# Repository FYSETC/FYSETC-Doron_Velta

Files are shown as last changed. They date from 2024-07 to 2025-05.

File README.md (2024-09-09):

# FYSETC-Doron Velta
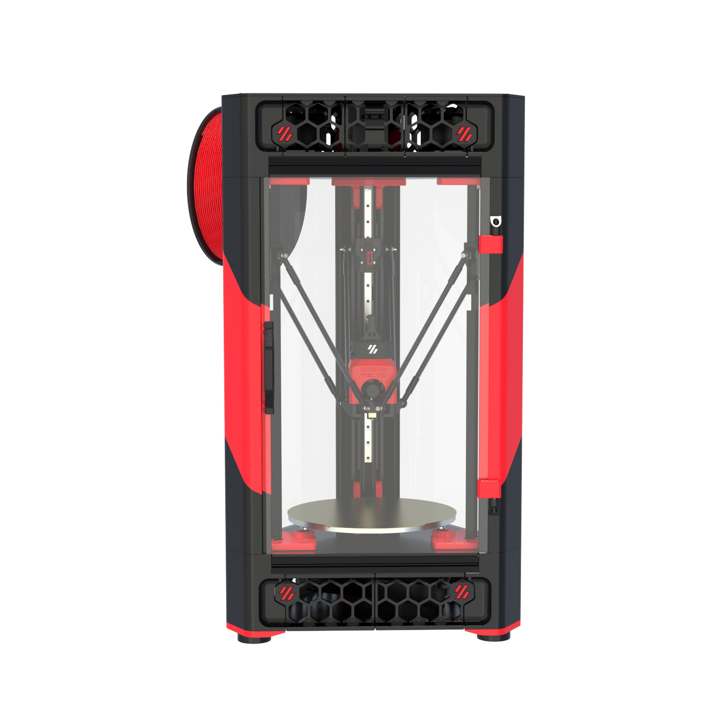
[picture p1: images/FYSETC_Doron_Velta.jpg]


## 1. Project

This is FYSETC's project database for Doron_Velta kit, which is convenient for you to find information. Thanks to rogerlz and everyone involved in this project, they always design fantastic printers.

Official Github：https://github.com/rogerlz/Doron-Velta

We make some small changes base on the Doron_Velta official material. Like change the board to R4 and others. 

## 2. Known issue

Please check your sensor cable before you power on the kit. The frst batch of sensor and endstop cables were shipped with wrong pinout. For the sensor cable, Use tweezers to change the wire on the right side of XH2.54 to the left, orthewise the sensor will be disabled.
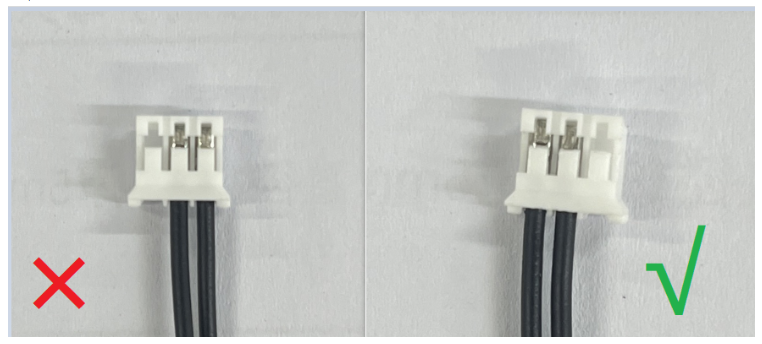
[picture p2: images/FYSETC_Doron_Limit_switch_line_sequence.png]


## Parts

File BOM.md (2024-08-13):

# Package list 

## Doron Velta 1.0

| Index | Sort | Component | Qty | Note |
| ----- | --- | --- | --- | --- |
| 1 | Fasteners | Doron Velta fasteners Pack | 1 SET  | |
| 2 | Frame | X/Y Pillars 2040 235mm | 6 PC | |
| 3 | Frame | Z Pillars 2020 500mm | 3 PCS  | |
| 4 | Motion | MGN9H Linear Rail and Carriage 350mm | 3 PCS  | |
| 5 | Motion | GATES GT2 Open Belt LL-2GT-9 (9mm wide) - 1200mm | 3 PCS  | |
| 6 | Motion | GT2 20T Pulley (5mm ID 9mm W) | 3 PCS  | |
| 7 | Motion | GT2 20T Toothed Idler (5mm ID 9mm W) | 3 PCS  | |
| 8 | Motion | Stainless steel spacer | 24 PCS | |
| 9 | Motion | Shaft Round 5x25mm (Idlers) | 3 PCS  | |
| 10 | Motion | Shaft Round 3x20mm (Bed) | 6 PCS  | |
| 11 | Motion | Washer M5x1.5mm | 8 PCS  | |
| 12 | Motion | Fisheye Rods 210mm | 6 PCS  | |
| 13 | Motion | M3 Teeth hole steel ball | 3 PCS  | |
| 14 | Vibration Management | Rubber Compressor Foot | 3 PCS  | |
| 15 | Buildplate | Aluminum plate platform - ∅200mm（Surface milling improve flatness） | 1 PCS  | |
| 16 | Buildplate | Scratch-proof Magnetic stickers ∅200mm thickness 1.5mm | 1 PCS  | |
| 17 | Buildplate | Hotbed Insulation cotton thickness 5mm | 1 PCS  | |
| 18 | Buildplate | PEI Film (∅200 mm) | 1 PCS  | |
| 19 | Buildplate | Hotbed Kit for ∅170mm 200W | 1 PCS  | |
| 20 | Controller | R4 V1.0 | 1 SET  | |
| 21 | Electronics | Raspberrypi 3B+/4B 2GB | 1 SET  | Optional |
| 22 | Electronics | MicroSD Card 16 GB | 1 PCS  | |
| 23 | Electronics | USB A to USB C - 1m | 1 PCS  | |
| 24 | Electronics | Round lamp beads | 2 PCS  | |
| 25 | Electronics | Klicky kit | 1 PCS  | |
| 26 | Electronics | Membrane level switch kit | 1 PCS  | |
| 27 | Electronics | NEMA17 Stepper motors 17HS8401 | 3 PCS  | |
| 28 | Electronics | Power Supply  Meanwell UHP-200R-24 | 1 PCS  | |
| 29 | Electronics | Raspberry Pi communication cable | 1 PCS  | |
| 30 | Electronics | Dual Ball FAN - 3010 24V (Part Fan) | 1 PCS  | |
| 31 | Electronics | Dual Ball FAN - 4010 24V(Hotend Fan) | 2 PC | |
| 32 | Electronics | Dual Ball FAN - 6020 24V (Ebox Fan) | 1 PCS  | |
| 33 | Electronics | Microswitch OMRON D2F-5 (Quickdraw Probe) with wire | 3 PCS  | |
| 34 | Electronics | Omron Solid State Relay | 1 PCS  | |
| 35 | Electronics | AC 3 Terminal Power Socket with Fuse | 1 SET  | |
| 36 | Electronics | C13 Power Cord | 1 PCS  | |
| 37 | Misc | Sherpa mini CNC Extruder | 1 SET  | |
| 38 | Misc | Wiring kit（Pre-crimped terminals and longer wire lengths with label） | 1 SET  | |
| 39 | Misc | Sailfish High Flow Hotend （ all-metal hotend 24V 60W) | 1 SET  | |
| 40 | Misc | Weaving casing 5mm 450mm | 1 PCS  | |
| 41 | Misc | Weaving casing 5mm 150mm | 2 PCS  | |
| 42 | Misc | Tension spring | 3 PCS  | |
| 43 | Misc | 4mm Bowden Coupler | 2 PCS  | |
| 44 | Misc | PTFE Tube (4mm OD 2mm ID) - 2m | 1 PCS  | |
| 45 | Misc | 6x3 Round Magnet (Quickdraw and Y Belt Set Tool) | 10 PCS | |
| 46 | Misc | Cutting pliers | 1 PCS  | |
| 47 | Misc | Hexagonal wrenchs | 1 SET  | |
| 48 | Misc | Thermal silica | 1 PCS  | |
| 49 | Misc | Ties | 30 PCS | |
| 50 | Misc | Foam Tape Thickness 3mm Length 4m | 1 PCS  | |
| 51 | Mics | The standby line 3m | 1 PCS  | |
| 52 | Misc | XH2.54 2/3/4 Pin Plastic shell | 1 SET  | |
| 53 | Panels | Bottom/Top/Electronics Bay Panels | 4 PCS  | |
| 54 | Panels | Side/Front Acrylic Panels | 3 PCS  | |

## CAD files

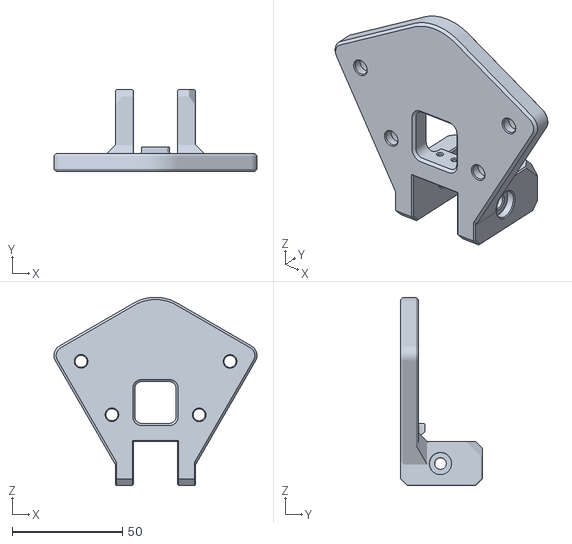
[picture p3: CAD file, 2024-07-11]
STLs/Bed Mount/Endstop Mount_x3.STL
92.1 x 37.0 x 85.5

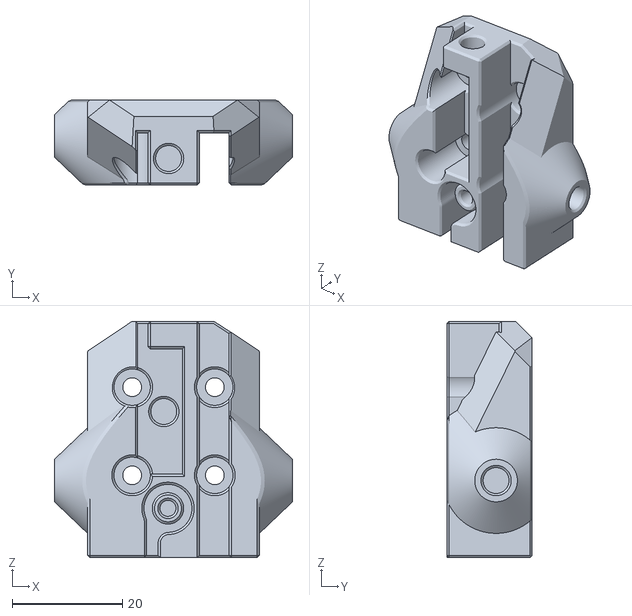
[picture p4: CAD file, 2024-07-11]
STLs/Carriage/Carriage v2_x3.STL
43.2 x 15.5 x 42.9

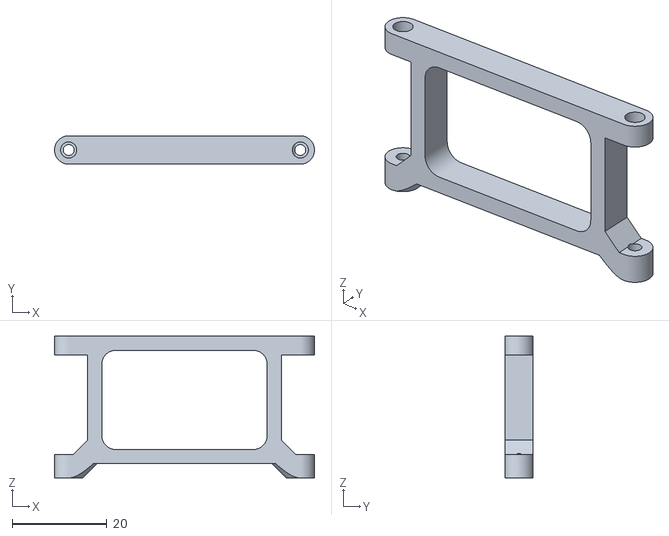
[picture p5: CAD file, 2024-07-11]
STLs/Control Board Rack/Raspberry Pi Stand_x2.STL
55.0 x 6.00 x 30.0

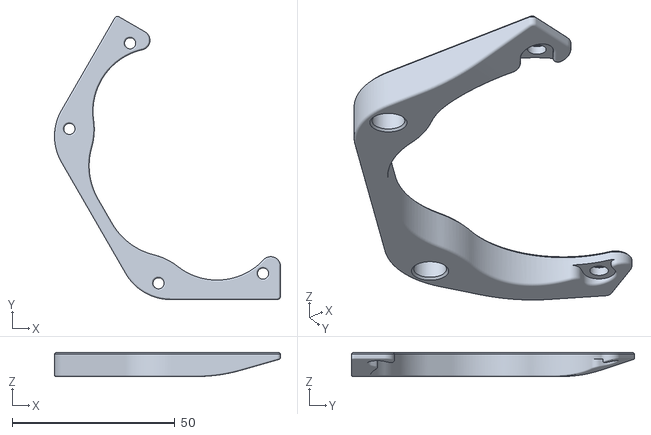
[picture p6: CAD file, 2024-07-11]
STLs/Corner Block/Foot Plate_x3.STL
69.5 x 87.1 x 7.40

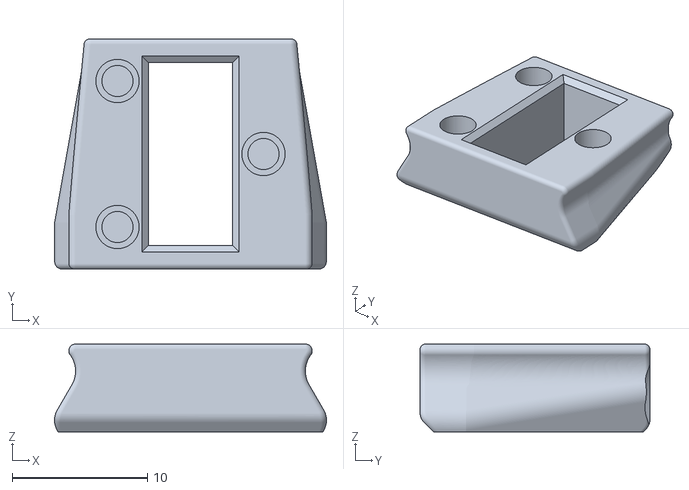
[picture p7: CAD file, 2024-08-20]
STLs/Extrude the head/printed_part.STL
20.1 x 17.0 x 6.50

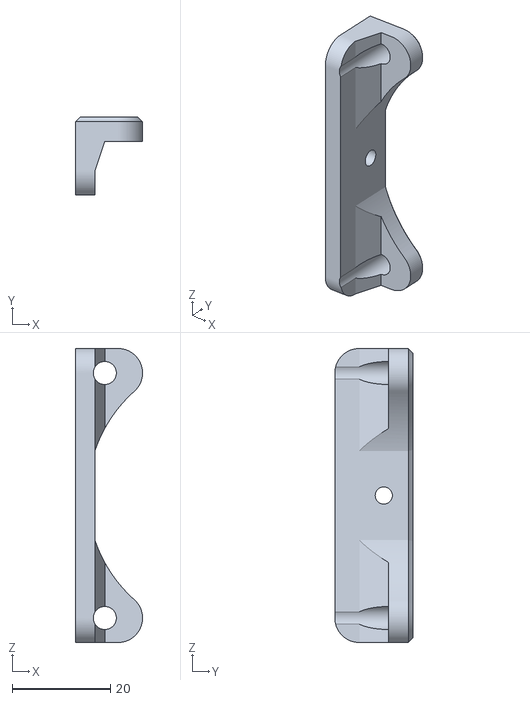
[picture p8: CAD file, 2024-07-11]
STLs/Fan/Fan Bracket_2.STL
13.7 x 16.0 x 60.0

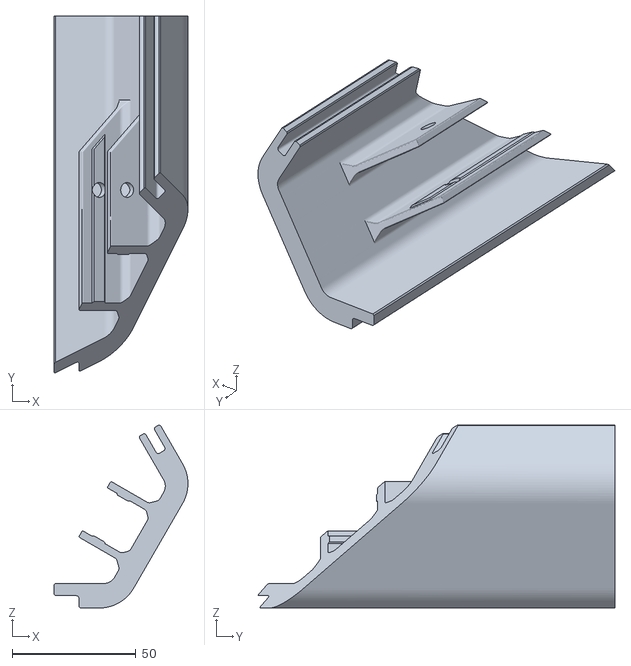
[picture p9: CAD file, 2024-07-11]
STLs/Middle Frame/Mid Corners (Mirror) Door_2_x1.STL
54.1 x 144.2 x 73.9

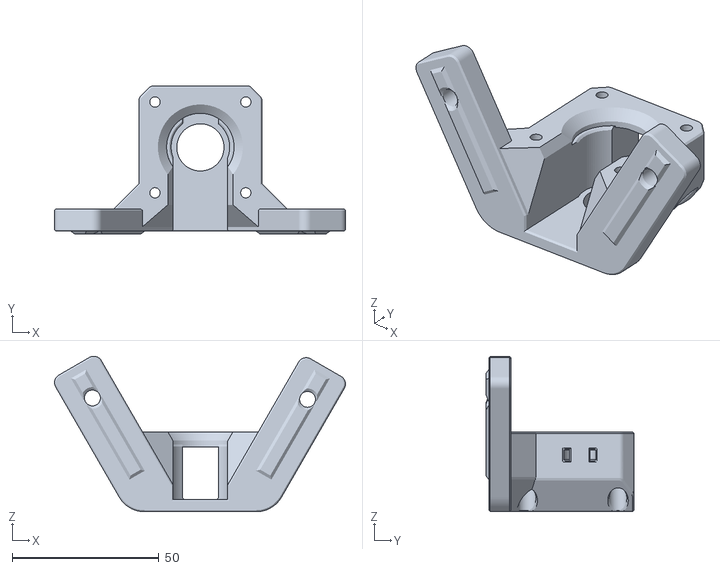
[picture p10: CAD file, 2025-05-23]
STLs/N17 Stepper Mount_x3.STL
99.3 x 50.6 x 53.0

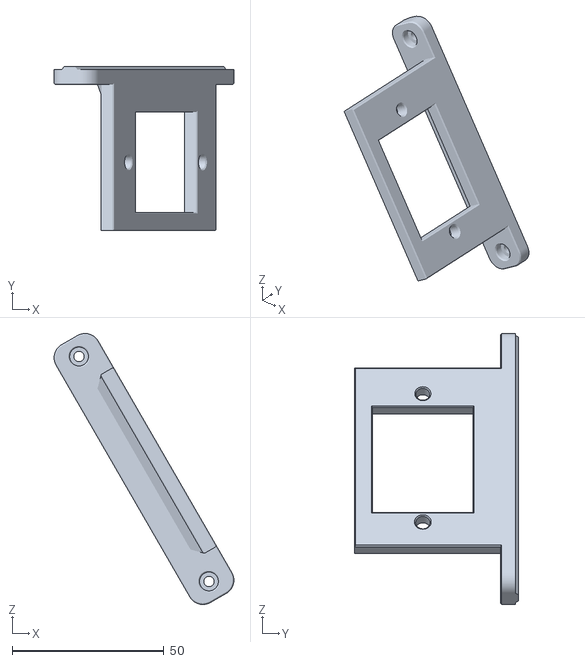
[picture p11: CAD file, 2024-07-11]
STLs/Power Supply/SSR_x1.STL
59.2 x 54.0 x 89.2

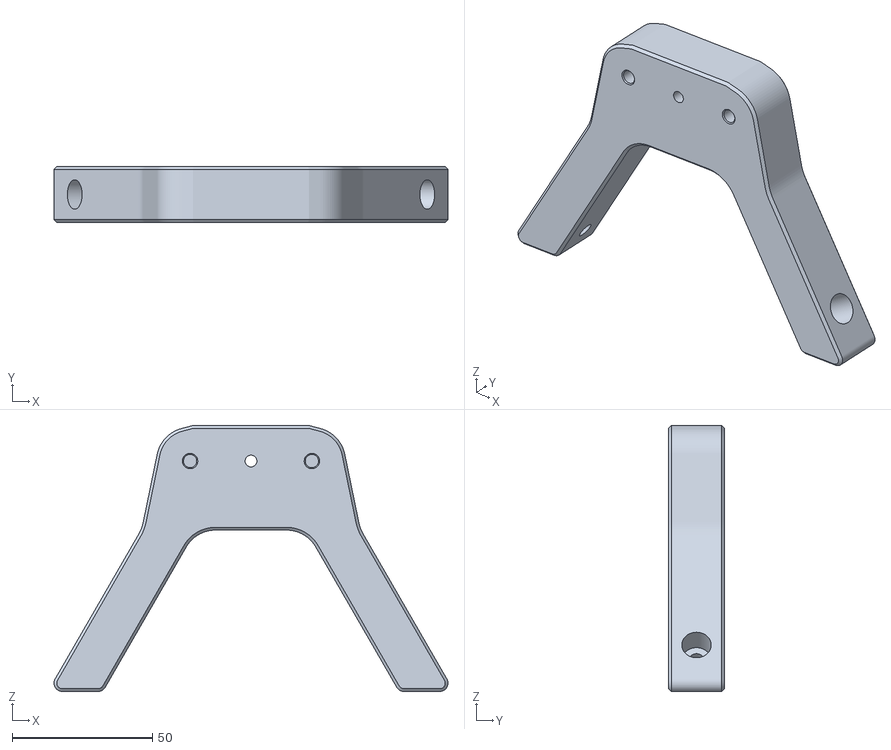
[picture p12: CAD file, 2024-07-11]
STLs/Sherpa/Bowden_Sherpa_x1.STL
140.7 x 20.0 x 95.0

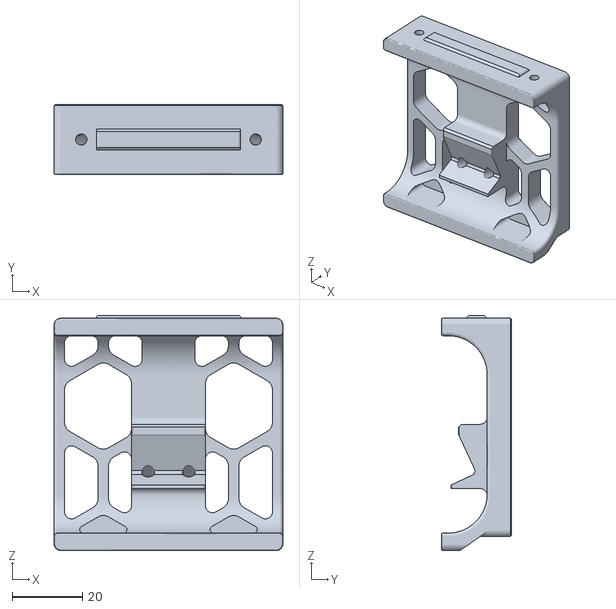
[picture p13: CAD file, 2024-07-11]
STLs/Skirt/Middle Of Top Skirt_1_x1.STL
65.0 x 20.0 x 66.8

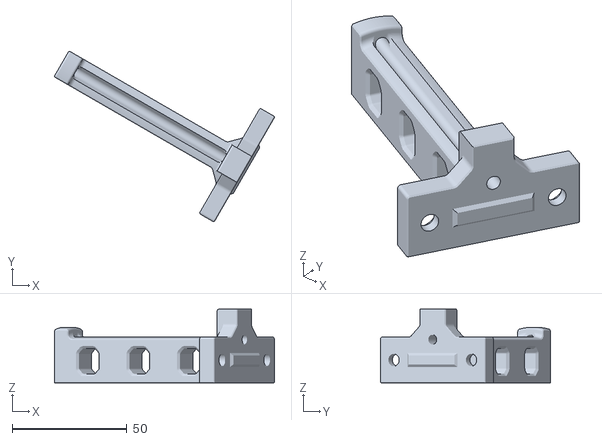
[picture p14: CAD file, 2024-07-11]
STLs/Spool Stand/SpoolHolder_x1.STL
95.8 x 74.2 x 32.2

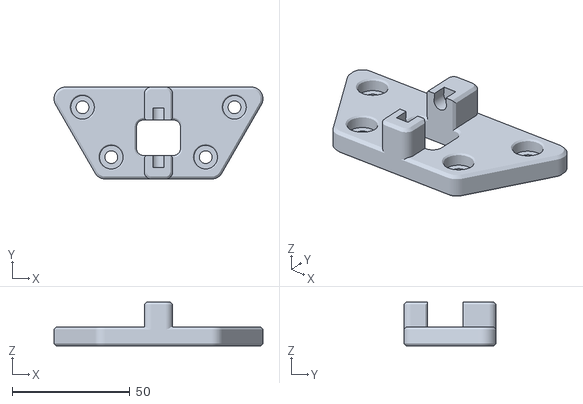
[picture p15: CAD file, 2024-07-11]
STLs/Z_Idlers/Idler Mount Mellow and Pin_x3.STL
88.6 x 39.0 x 18.6

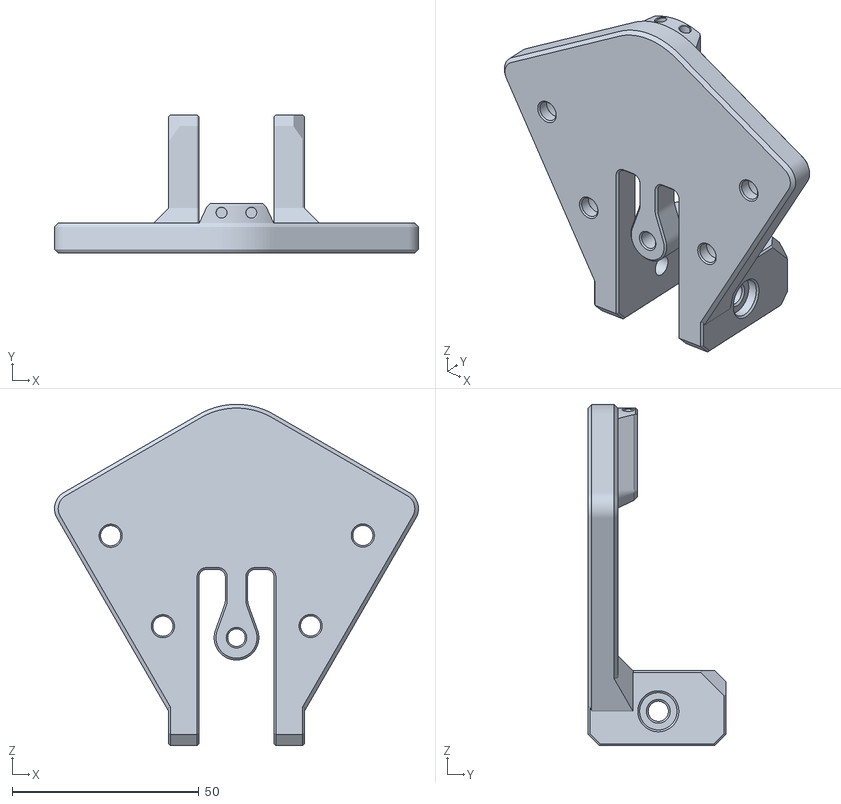
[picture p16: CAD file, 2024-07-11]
STLs/Bed Mount/Bed Mount_x3.STL
97.6 x 37.0 x 91.5

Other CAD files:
STLs/Carriage/_A__RAIL_GUARD_R1_0_x3.STL
STLs/Control Board Rack/Pico Mount_x1.STL
STLs/Corner Block/Lower Corner Block_x3.STL
STLs/Extrude the head/Effector_Cage_x1.STL
STLs/Carriage/Tensioner v2_x3.STL
STLs/Corner Block/Upper Corner Block_x3.STL
STLs/Extrude the head/Dragon_Mount.STL
STLs/Extrude the head/Effector_Plate_Nuts_x1.STL
STLs/Extrude the head/Lens_Carrier_x2.STL
STLs/Extrude the head/Lens（transparent）_x2.STL
STLs/Extrude the head/Strain_Relief_x1.STL
STLs/Fan/Fan Bracket_1.STL
STLs/Fan/Fan Grill A_x1.STL
STLs/Middle Frame/Door Hinge_1_x1.STL
STLs/Middle Frame/Door Hinge_2_x1.STL
STLs/Middle Frame/Mid Corners (Mirror) Door_1_x1.STL
STLs/Middle Frame/Mid Corners (Mirror) Door_3_x1.STL
STLs/Middle Frame/Mid Corners (Mirror) Door_4_x1.STL
STLs/Middle Frame/Mid Corners Flat_1_x2.STL
STLs/Middle Frame/Mid Corners Hinge_1_x1.STL
STLs/Middle Frame/Mid Corners Hinge_2_x1.STL
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

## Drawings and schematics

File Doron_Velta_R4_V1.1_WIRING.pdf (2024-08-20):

# Doron Velta

## HOT SURFACE

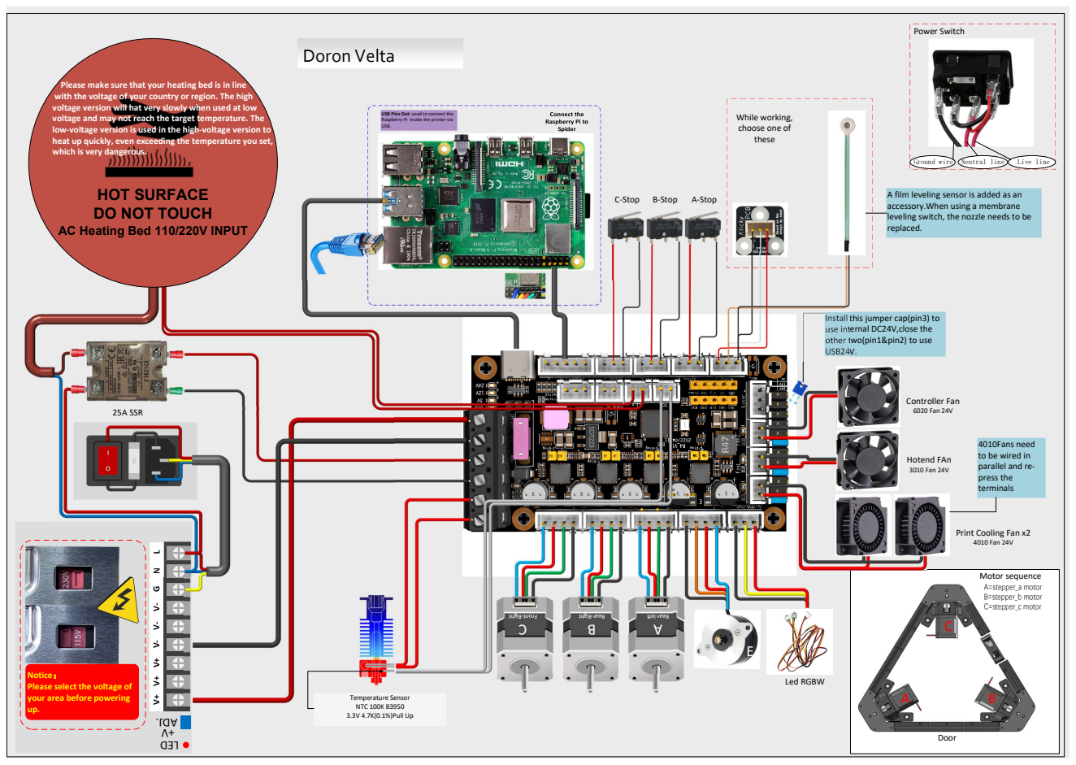
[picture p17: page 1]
Door; Motor sequence; LCD; 25A SSR; Temperature Sensor NTC 100K B3950 3.3V 4.7K(0.1%)Pull Up; Hotend FAn 3010 Fan 24V; Led RGBW; Controller Fan 6020 Fan 24V; C-Stop B-Stop; A-Stop; A=stepper_a motor B=stepper_b motor C=stepper_c motor; Power Switch; Ground wire Neutral line; Live line

Please make sure that your heating bed is in line
with the voltage of your country or region. The high
voltage version will hat very slowly when used at low
voltage and may not reach the target temperature. The
low-voltage version is used in the high-voltage version to
heat up quickly, even exceeding the temperature you set,
which is very dangerous.

USB Pins Out: used to connect the Raspberry Pi inside the printer via USB.

While working,
choose one of
these

A film leveling sensor is added as an
accessory.When using a membrane
leveling switch, the nozzle needs to be
replaced.

DO NOT TOUCH
AC Heating Bed 110/220V INPUT

Install this jumper cap(pin3) to
use internal DC24V,close the
other two(pin1&pin2) to use
USB24V.

4010Fans need
to be wired in
parallel and re-
press the
terminals

Print Cooling Fan x2
4010 Fan 24V

Notice： Please select the voltage of

your area before powering

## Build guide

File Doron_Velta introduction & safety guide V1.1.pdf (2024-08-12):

V1.0 | Powered by Doron Velta, Produce by FYSETC | www.fysetc.com

# Product Introduction

Thank you for purchasing Doron Velta 3D printer kit from FYSETC (no printed parts included).
You can download the print parts at https://github.com/FYSETC/FYSETC-Doron_Velta/tree/main/STLs

In case of any printer-related problem, do not hesitate to contact our customer service. We are glad to receive all of your valuable comments and tips. More product info here: https://github.com/FYSETC/FYSETC-Doron_Velta

## Product details

Mechanical structure:
- Frame: aluminum box structure
- Printing platform: 6061 thickened aluminum
- Plate: elastic powder steel plate
Print parameters:
- Printing technology: FDM
- Build volume: ∅ 1 40x 160mm（Sealing） /170x160mm（No Sealing）
- Printing layer height: 0.05-0.3mm (use 0.4mm nozzle)
- Maximum printing speed: 200mm/s (recommended: 20-80mm /s)
- Filament diameter: 1.75mm
- Nozzle diameter: 0.4mm
- Filament types: PLA, PETG, PLA-CF carbon fiber, ABS, TPU, HIPS, WOOD, etc. (The default printing parameter is for PLA, and other filaments should be adjusted according to the parameters provided by the filament supplier.)
Temperature:
- Maximum extruder temperature: 300°C
- Maximum temperature of hot bed: 120°C

Software parameters:
- Firmware: Klicky kit,Membrane level switch
- Supported formats: STL, G-code, AMF, OBJ
- Input mode: Ethernet, WiFi
- Operating software: Simplify3d, PrusaSlicer, Cura, Repeater host
- Operating system: Windows 7/ Mac OS / Linux Hardware parameters:
- WiFi: support (Based on Raspberry Pi)
- Controller : R4+ Raspberry Pi 3/4
- Power supply: Meanwell LRS-200-24
- Input: 100-120V,4.0A / 200-240V, 2.0A Size & weight:
- Machine size: 344x360x625mm
- Package size: 625x415x155mm
- Net weight of machine: 10.2kg

## Disclaimer

Failure to read the assembly descriptions may lead to personal injury, inferior results, or damage to the 3D printer. Always ensure that anyone who operates the 3D printer knows and understands the operation description. We cannot control the conditions in which you assemble the kit. For this, and other reasons, we do not assume responsibility, and expressly disclaim liability for loss, injuries, damage, or expense arising out of, or in any way connected with, the assembly, handling, storage, use or disposal of the product. The information in this handbook is provided without any warranty, expressed or implied, regarding its correctness.

## Licenses

VORON 2.4 R2 printer is a part of the VoronDesign project, the first open-source 3D printer project free to use under a GNU General Public License v3.0 license (www.gnu.org/licenses/gpl-3.0.en.html).

Permissions: Commercial use, Modification, Distribution, Patent use, Private use

Limitations: Liability, Warranty

V1.0 | Powered by Doron Velta, Produce by FYSETC | www.fysetc.com

# Safety Guide

Read and understand the assembly manual and safety instructions before beginning to assemble and use the kit. Failure to do so may result in serious injury or death. Save this document.

Please be very cautious during any interaction with the printer. This printer is an electrical device with moving parts and hot-temperature areas.

## Assembly

- Never disassemble the printer's power supply: it does not contain any parts that can be - repaired by unskilled workers. All repairs must be carried out by qualified technicians.
- In the process of assembling and using the printer, please be careful not to touch or go deep into the moving position to avoid scratching or pinching.
- Adult supervision required: Prevent children from touching printer parts or printers unattended, even if the printer is not assembled or printed. Observe children closely and intervene if necessary to prevent potential safety issues and ensure proper use of the printer. Ensure that young children cannot touch small 3D printed parts or 3D printed parts. These are potential suffocation hazards for young children.

## Wiring

- Before starting the wiring, please read the wiring diagram carefully, understand the installation method of each position, confirm the positive and negative positions, especially confirm that the AC wiring of the PSU is correct and there is no short circuit. The inspection is to observe the wiring position instead of just looking at the color.
- Please make sure that all electronic wires are not damaged mechanically or otherwise. If so, please stop using the damaged electronic wire immediately and replace it.
- Before powering on for the first time, please make sure that you have selected the input voltage of the PSU according to your area, otherwise the PSU will be severely burned, or even other peripherals such as the motherboard, and cannot be repaired.

## Use

- The printer is for indoor use only. Do not expose the printer to rain or snow. Always place the printer in a dry environment and keep at least 30 cm away from other objects.
- Always place the printer in a stable place to prevent it from falling or tipping over.
- After the machine is debugged, you must be on duty throughout the printing process to avoid malfunctions. In several cases, it may cause a fire. Please do not leave the printer unattended when the printer is turned on!
- When you unplug the power cord from the socket, pull the plug instead of the power cord to reduce the risk of damaging the plug or AC power outlet.
- During the process of setting up and operating the printer, the printing platform and the printing nozzle are at a high temperature. Avoid direct contact with these areas. The nozzle temperature is 190-300°C (374-572°F); the heating bed temperature can reach above 100 °C (212 °F). Temperatures higher than 40 °C (104 °F) can cause harm to the human body.
- The plastic melts during the printing process and produces a peculiar smell. Put the printer in a well-ventilated place.

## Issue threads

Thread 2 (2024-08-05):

Print Start/End Macro?

hreality, 2024-08-05:
Could you share the applicable start/end macros please

zzcatvs, 2024-08-16:
OrcaSlicer

Start Gcode：
`G21
G90
M82
G28 ; home all axes
M140 S[first_layer_bed_temperature]
M104 S[first_layer_temperature] T0
G1 F3000 Z1
G1 X-78 Y0 Z0.4
M107 T0
M109 S[first_layer_temperature] T0
M190 S[first_layer_bed_temperature]
G92 E0
G3 X0 Y-78 I78 Z0.3 E30 F2000
G92 E0`

End Gcode：
`M107
M104 S0
M140 S0
G92 E1
G1 E-1 F300
G28 X0 Y0
;M84
M18 S180 ;disable motors after 180s
`

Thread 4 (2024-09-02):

Door_handle_x1.stl is missing

yettiz, 2024-09-02:
The door handle is missing.
Found it on rogerlz's website.

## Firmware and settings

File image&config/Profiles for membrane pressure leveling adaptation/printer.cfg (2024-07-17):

#   ________________.___. ________________________________________  
#   \_   _____/\__  |   |/   _____/\_   _____/\__    ___/\_   ___ \ 
#    |    __)   /   |   |\_____  \  |    __)_   |    |   /    \  \/ 
#    |     \    \____   |/        \ |        \  |    |   \     \____
#    \___  /    / ______/_______  //_______  /  |____|    \______  /
#        \/     \/              \/         \/                    \/ 

#########################################################################
# Printer: Doron-Velta R2                            MCU: Fysetc R4 v1  #
#########################################################################

# For more info check https://github.com/FYSETC/FYSETC-R4
# For more printer info check https://github.com/rogerlz/Doron-Velta
# For more firmware info check https://dangerklipper.io
# See docs/Config_Reference.md for a description of parameters.

## Doron-Velta R2 Fysetc-R4 1.0 config V1.0

#########################################################################
# Firmware configuration with "make menuconfig" for Fysetc R4 v1 :      #
#                                                                       #
# [*] Enable extra low-level configuration options                      #
#     Micro-controller Architecture (Raspberry Pi RP2040)  --->         #
#     Communication interface (USB)  --->                               #
#     USB ids  --->                                                     #
# ()  GPIO pins to set at micro-controller startup                      #
#########################################################################
# Firmware upload ：
## Step 1: Power on the board
## Step 2: Connect R4 to your computer with USBC cable
## Step 3: Push an hold BOOTSEL button
## Step 4: Click RST button and release BOOTSEL button
## Step 5: RPI-RP2 folder will show up on your computer, copy klipper.uf2 to the folder.

########################################
# MCU Settings
########################################

[mcu]
serial: /dev/serial/by-id/usb-Klipper_rp2040_E661AC8863596726-if00
# To find your USB serial addres run: ls /dev/serial/by-id/*

[temperature_sensor Raspberry_Pi]
sensor_type: temperature_host
min_temp: 1
max_temp: 100

[temperature_sensor Fysetc_R4]
sensor_type: temperature_mcu
min_temp: 0
max_temp: 100


########################################
# Printer Settings
########################################

[printer]
kinematics: delta
max_velocity: 50
max_accel: 1500
max_z_velocity: 50
minimum_z_position: -25
delta_radius: 100.922298
print_radius: 100


########################################
# X Stepper Motor & Driver Settings
########################################

[stepper_a]
step_pin: gpio3
dir_pin: gpio2
enable_pin: !gpio4
rotation_distance: 40
microsteps: 16
endstop_pin: ^gpio11
homing_speed: 20
homing_retract_dist: 5
homing_retract_speed: 10
position_endstop: 170
angle: 209.197966
arm_length: 215

[tmc2209 stepper_a]
uart_pin: gpio9
tx_pin: gpio8
uart_address: 1   
interpolate: True
run_current: 0.8
hold_current: 0.6
sense_resistor: 0.220
stealthchop_threshold: 999999


########################################
# Y Stepper Motor & Driver Settings
########################################

[stepper_b]
step_pin: gpio16
dir_pin: gpio15
enable_pin: !gpio14
rotation_distance: 40
microsteps: 16
endstop_pin: ^gpio12
position_endstop: 170
angle: 328.568677
arm_length: 215

[tmc2209 stepper_b]
uart_pin: gpio9
tx_pin: gpio8
uart_address: 2
run_current: 0.8
hold_current: 0.6
sense_resistor: 0.220
stealthchop_threshold: 999999


########################################
# Z Stepper Motor & Driver Settings
########################################

[stepper_c]
step_pin: gpio19
dir_pin: gpio18
enable_pin: !gpio17
rotation_distance: 40
microsteps: 16
endstop_pin: ^gpio13
position_endstop: 170
angle: 90
arm_length: 215

[tmc2209 stepper_c]
uart_pin: gpio9
tx_pin: gpio8
uart_address: 3
run_current: 0.580
hold_current: 0.500
sense_resistor: 0.220
stealthchop_threshold: 999999


########################################
# Extruder & Driver Settings
########################################

[extruder]
step_pin: gpio6
dir_pin: gpio5
enable_pin: !gpio7
heater_pin: gpio24
sensor_pin: gpio26
sensor_type: EPCOS 100K B57560G104F
microsteps: 16
rotation_distance: 3.584
full_steps_per_rotation: 200
smooth_time: 3
min_temp: -270
max_temp: 310
min_extrude_temp: 170
nozzle_diameter: 0.400
filament_diameter: 1.750
max_extrude_only_distance: 1000.0
max_extrude_only_velocity: 120
max_extrude_cross_section: 5
pressure_advance: 0.02
pressure_advance_smooth_time: 0.02
instantaneous_corner_velocity: 1.000
control: pid
pid_kp: 30.684
pid_ki: 2.188
pid_kd: 107.585

[tmc2209 extruder]
uart_pin: gpio9
tx_pin: gpio8
uart_address: 0
interpolate: True
run_current: 0.650
hold_current: 0.500
sense_resistor: 0.220
stealthchop_threshold: 999999


########################################
# Bed Settings
########################################

[heater_bed]
heater_pin: gpio23
sensor_type: EPCOS 100K B57560G104F
sensor_pin: gpio27
max_power: 1
min_temp: -100
max_temp: 130
control: pid
pid_Kp: 325.10
pid_Ki: 63.35
pid_Kd: 417.10


########################################
# Probe Settings
########################################

[probe]
pin: !gpio10 
x_offset: 0
y_offset: 0
z_offset: 0.16
speed: 10
samples: 3
samples_result: median
sample_retract_dist: 3
samples_tolerance: 0.01
samples_tolerance_retries: 5


########################################
# Delta Calibration & Mesh Settings
########################################

[delta_calibrate]
radius: 80
horizontal_move_z: 15

[bed_mesh]
speed: 50
horizontal_move_z: 15
mesh_radius: 80
mesh_origin: 0,0
round_probe_count: 5
algorithm: bicubic


########################################
# Fans Settings
########################################

[fan]
pin: gpio20

[heater_fan Pi_fan]
pin: gpio22
heater: extruder
fan_speed: 0.5
heater_temp: 50.0

[heater_fan hotend_fan]
pin: gpio21
heater: extruder
heater_temp: 50.0


########################################
# LED Settings
########################################

[neopixel LED_Hotend]
pin: gpio29
chain_count: 2
color_order: GRBW
initial_RED: 0.0
initial_GREEN: 0.0
initial_BLUE: 0.0
initial_WHITE: 1.0


##################################################
# Pause / Resume / Cancel Print
##################################################

[gcode_macro PAUSE]
description: Pause the actual running print
rename_existing: PAUSE_BASE
gcode:
    ##### set defaults #####
    {% set x = params.X|default(0) %}      #edit to your park position
    {% set y = params.Y|default(-67) %}      #edit to your park position
    {% set z = params.Z|default(10)|float %} #edit to your park position
    {% set e = params.E|default(1) %}        #edit to your retract length

    ##### calculate save lift position #####
    {% set max_z = printer.toolhead.axis_maximum.z|float %}
    {% set act_z = printer.toolhead.position.z|float %}
    {% set lift_z = z|abs %}
    {% if act_z < (max_z - lift_z) %}
        {% set z_safe = lift_z %}
    {% else %}
        {% set z_safe = max_z - act_z %}
    {% endif %}

    ##### end of definitions #####
    PAUSE_BASE
    G91
    {% if printer.extruder.can_extrude|lower == 'true' %}
      G1 E-{e} F2100
    {% else %}
      {action_respond_info("Extruder not hot enough")}
    {% endif %}
    {% if "xyz" in printer.toolhead.homed_axes %}    
      G1 Z{z_safe}
      G90
      G1 X{x} Y{y} F6000
    {% else %}
      {action_respond_info("Printer not homed")}
    {% endif %}

[gcode_macro RESUME]
description: Resume the actual running print
rename_existing: RESUME_BASE
gcode:
    ##### set defaults #####
    {% set e = params.E|default(1) %} #edit to your retract length
    #### get VELOCITY parameter if specified ####
    {% if 'VELOCITY' in params|upper %}
      {% set get_params = ('VELOCITY=' + params.VELOCITY)  %}
    {%else %}
      {% set get_params = "" %}
    {% endif %}
    ##### end of definitions #####
    G91
    {% if printer.extruder.can_extrude|lower == 'true' %}
      G1 E{e} F2100
    {% else %}
      {action_respond_info("Extruder not hot enough")}
    {% endif %}   
    RESUME_BASE {get_params}

[gcode_macro CANCEL_PRINT]
description: Cancel the actual running print
rename_existing: CANCEL_PRINT_BASE
gcode:
  RESPOND MSG="Printing canceled"
  G28
  M106 S0
  M104 S0
  M140 S0
  CANCEL_PRINT_BASE

########################################
# G-Code Macros & Events
########################################

[virtual_sdcard]
path: /home/pi/printer_data/gcodes
on_error_gcode: CANCEL_PRINT

[idle_timeout]
timeout: 1800

[gcode_arcs]
resolution: 0.1

[respond]

[pause_resume]

[display_status]


########################################
# Danger Settings
########################################

[danger_options]
log_statistics: False
log_config_file_at_startup: False
log_bed_mesh_at_startup: False

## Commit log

2024-07-11 Add files via upload
    1. Project
    This is FYSETC's project database for Doron_Velta kit, which is convenient for you to find information. Thanks to rogerlz and everyone involved in this project, they always design fantastic printers.
    Official Github：https://github.com/rogerlz/Doron-Velta
    We make some small changes base on the Doron_Velta official material. Like change the board to R4 and others.
2024-07-11 Update file
    Upload stls file
    [Bed Mount_x3.STL, Bottom Skirt Left_x3.STL, Bottom Skirt Power_x1.STL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]
2024-07-11 Data update
    Upload BOM
2024-07-17 add cad file
2024-08-12 Update BOM.md
    Corrected specifications and models
2024-08-13 Update BOM.md
    BOM update
2024-08-20 Update power switch wiring sequence
2024-08-20 Added Klicky printables
    [printed_part.STL]
2024-09-09 Add files via upload
    Limit switch line sequence
2025-05-23 Data Update
    [N17 Stepper Mount_x3.STL]
